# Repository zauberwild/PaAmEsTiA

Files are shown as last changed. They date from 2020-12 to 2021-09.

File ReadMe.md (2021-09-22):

Paamestia
=========
_Teammitglieder: Max, Dominik, André, Arvid

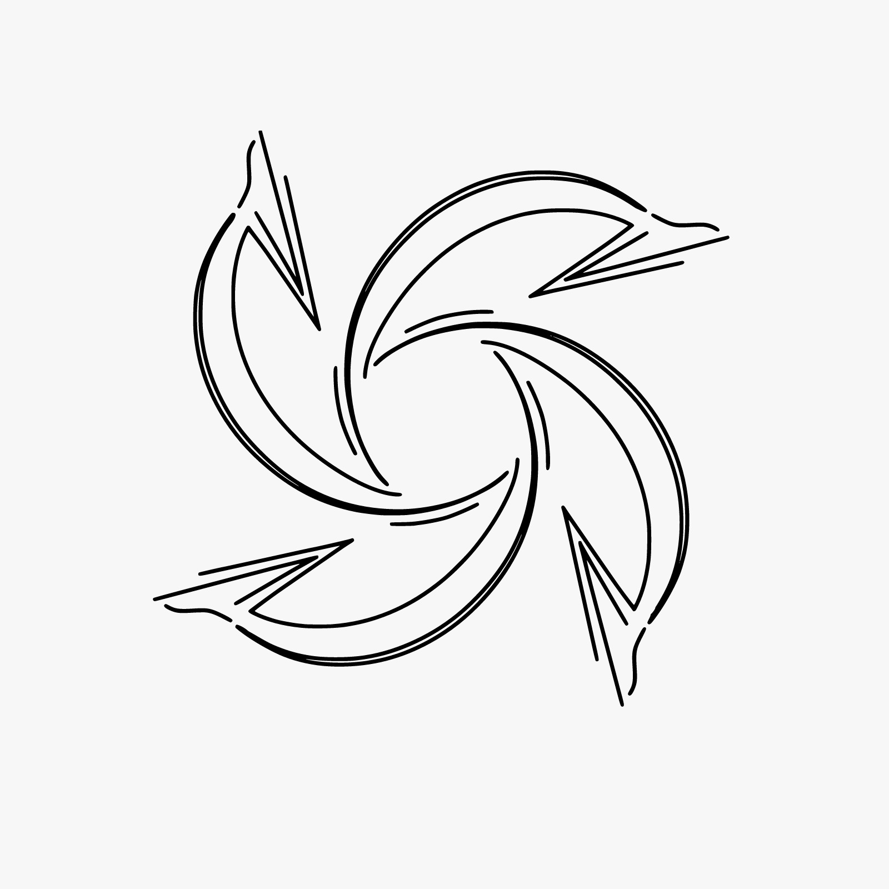
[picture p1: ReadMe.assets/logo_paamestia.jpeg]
logo_paamestia


Info
----

In diesem Repository sind alle Dateien, Quellcodes, etc. für das Praxisprojekt für Fach Praxis im BGT an der BBS.  

Bei dem Projekt handelt es sich um eine Cocktail-Mischmaschine, bei der man ein Rezept auswählt und dies automatisch gemischt wird.
Außerdem soll es möglich sein, selber frei zu mischen und Rezepte zu importieren. 

---

Software (./code)
-----------------
Geschrieben wurde der Quellcode in Python, da diese relativ einfach anzuwenden ist und für den Raspberry Pi gut geeignet ist
Der Quellcode besteht aus mehreren Dateien, denen verschiedenen Aufgaben zukommen. Die Datei media_lib.py kümmert sich um alles grafische und was die Darstellung betrifft, io_lib.py kümmert isch um den direkten Input (Taster) und Output (Ventile und Pumpe) und drinks_lib.py ist u.a. für die Verwaltung der Rezepte und Getränke zuständig. Genauere Informationen zu dem Quellcode finden sich außerdem im Ordner `/documentation/Sourcecode + System`.  

---

Hardware
--------
Das Hirn des gesamten Projekts ist ein Raspberry Pi, einem Einplatinencomputer, der neben Standard-Anschlüssen, wie USB und HDMI auch über GPIO-Pins (_**G**eneral-**P**urpose-**I**nput-**O**uput-Pins_) verfügt. Diese werden dazu verwendet um die Taster auszulesen, und die Ventile anzusteuern. Die Ansteuerung erfolgt dabei über zwei Relais-Boards, um die hohe Stromaufnahme nicht direkt über den Raspberry Pi zu leiten.  
Für das Bild wird ein alter 3/4-Monitor verwendet, auf dem die grafische Benutzeröberfläche angezeigt wird.  
Die Stromversorgung gestaltete sich etwas schwieriger, weil die Pumpe und Ventile mit 12V betrieben werden müssen, Der RasPi aber nur mit 5V. Dafür wurde erst ein 12V-Netzteil verwendet, und zusätzlich ein Step-Down-Converter, der die Spannung für den RasPi auf 5V runterregelt.  
Zur Konstruktion wurden Alu-Profile als Rahmen verwendet, für die Abdeckung Blech. Zur Montage einiger Bauteile wurden außerdem Halterungen 3D-gedruckt, verwendet wurde dafür der Anycubic Mega S mit dunkelgrauem PETG und blauem PLA.  
_Weitere Informationen, Schematiken und CAD-Dateien sind im `documentation`-Ordner zu finden_

### BOM  
In dieser Liste sind hauptsächlich nur die elektronischen und mechanischen Bauteile aufgelistet. Zusätzliche Meterialien, wie Alu-Profil-Schienen werden natürlich ebenfalls benötigt.

- Raspberry Pi 3(b) ([Amazon](https://www.amazon.de/Raspberry-Pi-Model-ARM-Cortex-A53-Bluetooth/dp/B01CD5VC92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))
- Magnetventile (6 Stück, Öffner)
- Schlauch
- Schlauchverbinder
- Relais-Board (insgesamt 7 Relais, [Amazon](https://www.amazon.de/AZDelivery-8-Relais-Optokoppler-Low-Level-Trigger-Arduino/dp/B07CT7SLYQ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ÅMÅŽÕÑ&crid=1XKVNJ5KDLTPH&dchild=1&keywords=azdelivery+relay&qid=1607777597&sprefix=azdeliver%2Caps%2C275&sr=8-8))
- Schlauchpumpe ([Amazon](https://www.amazon.de/Schlauchpumpe-Flüssigkeitspumpe-Schlauchwasserpumpe-Silikonschlauch-Pharmazeutika/dp/B07TVDXJQN))
- Silikonstopfen ([Amazon](https://www.amazon.de/Tuuters-Silikonstopfen-Konische-Abdeckstopfen-Gummistopfen/dp/B01LWOXOLZ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ÅMÅŽÕÑ&crid=11L4LGF9305AW&dchild=1&keywords=silikonstopfen&qid=1607778777&sprefix=silikonstopf%2Caps%2C253&sr=8-5&th=1))
- Taster (6 Stück)
- 12 V Netzteil ([Amazon](https://www.amazon.de/Netzteil-Transformator-Universelles-AC110-240V-Geeignet/dp/B0871TVVRR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))
- Step-Down-Converter (aus eigenem Lagerbestand, zu finden aber zum Beispiel hier: [Amazon](https://www.amazon.de/Stromversorgung-Spannungsregler-Abw%C3%A4rtswandler-Hocheffizienter-Einstellbares/dp/B07F38DJLS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))

Filamente:  
- [DasFilament PETG Anthrazit](https://www.dasfilament.de/filament-spulen/petg-1-75-mm/438/petg-filament-1-75-mm-anthrazit-v2?c=21)
- [Janbex PLA Blau](https://www.amazon.de/JANBEX-Filament-Drucker-Vakuumverpackung-Schwarz/dp/B08MC7LQZR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)

Credits
-------

Dieses Projekt steht unter der MIT-Lizenz (komplette Lizenz [hier](https://github.com/zauberwild/paamestia/blob/main/LICENSE))

### verwendete Module:

- [`pygame`](https://www.pygame.org/news) (und `pygame.freetype`)
- [`opencv`](https://opencv.org/) (und [`numpy`](https://numpy.org/))
- [`tkinter`](https://docs.python.org/3/library/tkinter.html)
- `os`, `time` und `pathlib`
- [`gpiozero`](https://github.com/gpiozero/gpiozero)

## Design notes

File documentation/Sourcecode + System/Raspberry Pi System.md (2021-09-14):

# Raspberry Pi System

## Autostart des Skripts

"Desktop"-Datei (Pfad: `/home/pi/.config/autostart/paamestia-auto.desktop`):  

`[Desktop Entry]`
`Name=Paamestia-Auto`
`Comment=Autostart Script for PaAmEsTiA`
`Type=Application`
`Exec=python3 /home/pi/paamestia/code/paamestia.py`
`Terminal=true`

## Steuerung

Wird mittels Datei `code/src/.windows` angeschaltet

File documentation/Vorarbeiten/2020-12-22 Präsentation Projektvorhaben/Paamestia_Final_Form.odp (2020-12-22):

## Project: Paamestia

Ein Projekt von:

Andre Milling, Dominic Kosin,

Arvid Randow und Max Schiemann

## Gliederung

- Überblick
- Technische Zeichnungen
- Programmierung
- Design
- Netzplan
- Materialliste + -kosten

## Überblick

- Getränkemischmaschine
- Erweiterbare Rezeptliste
- Getränke mischen
  - Nach Rezept
  - Nach Mischverhältnis

## 3D-modell

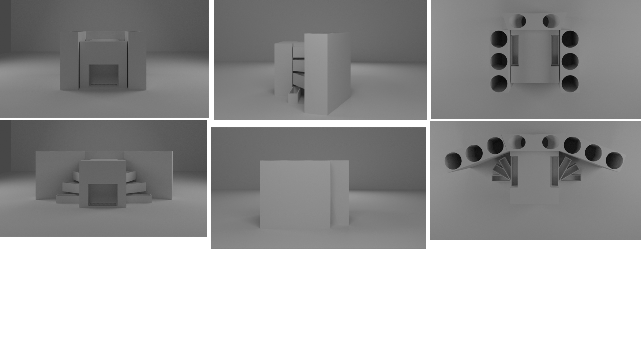
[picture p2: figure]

## Technische Zeichnungen

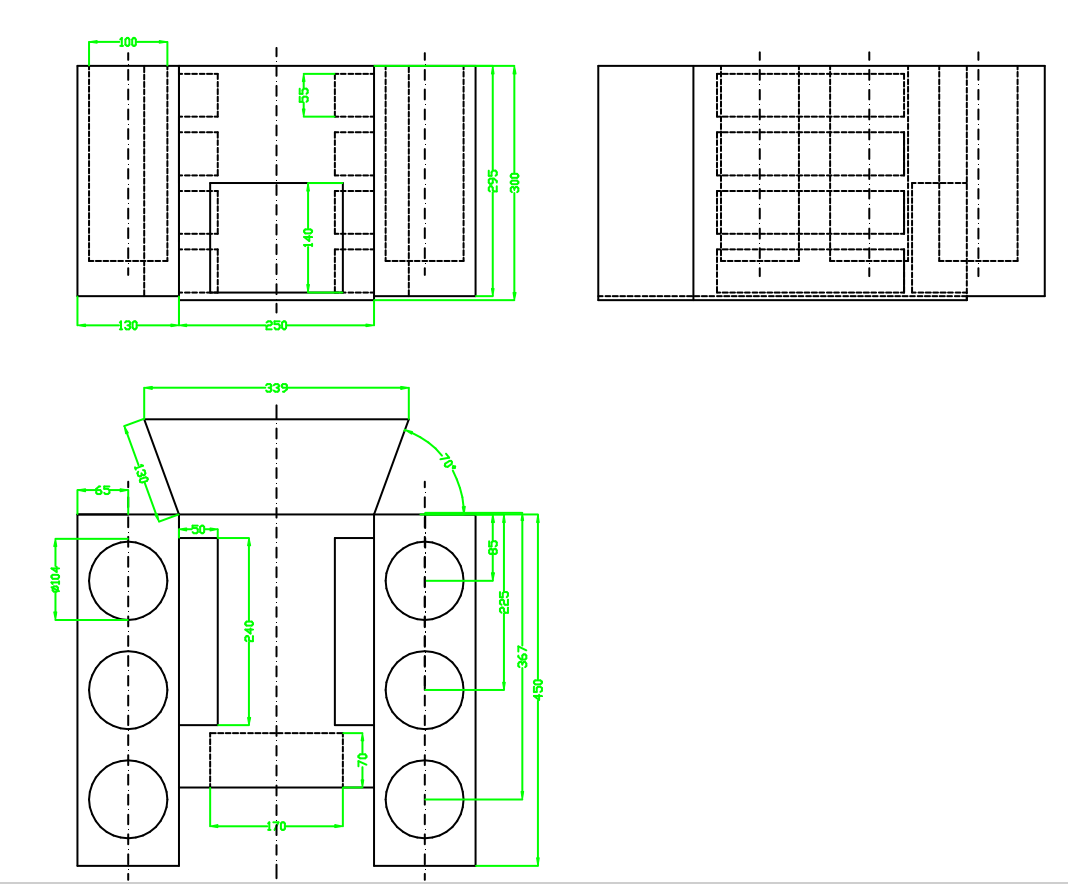
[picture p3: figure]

## Kontaktplan

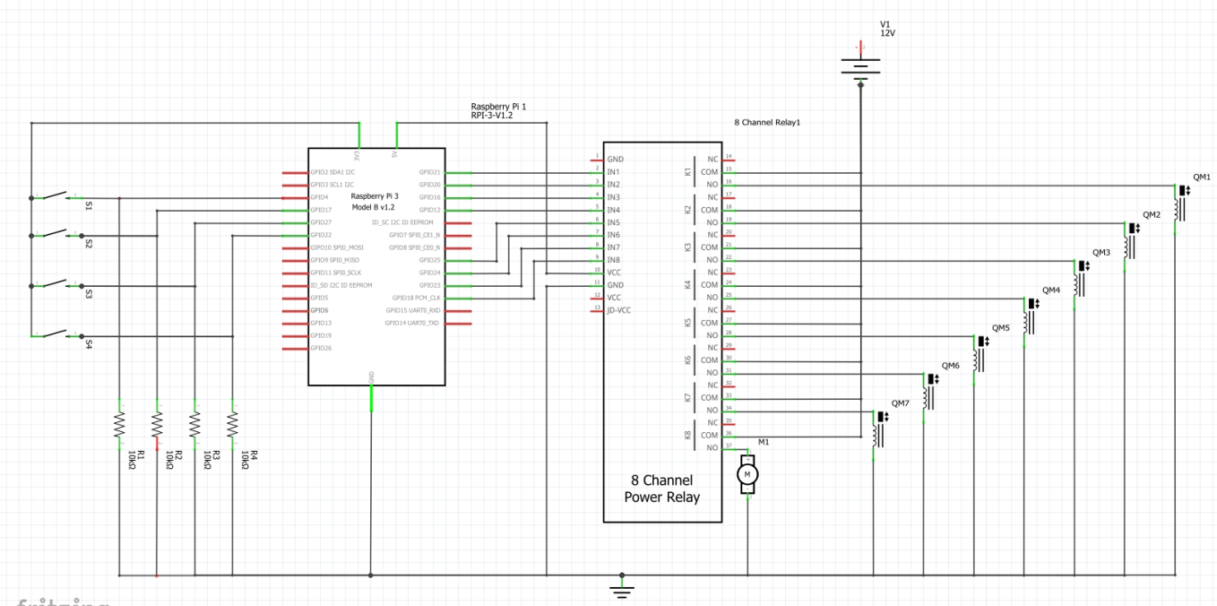
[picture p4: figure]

## Programmierung

- Aufbau
  - Einstellungen (Auswahl von angeschlossenen Getränken)
  - Rezeptauswahl
  - Frei mischen

## Design

- Bar Design
- Barkeeper leitet einen durchs Programm

## Zeitliche Planung

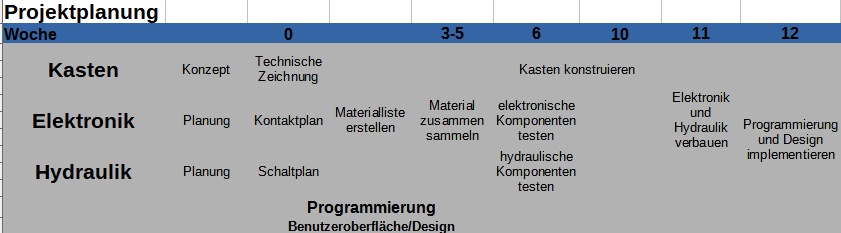
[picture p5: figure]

## Material+ -kosten

Teil | Stückpreis | Menge | Gesamtpreis
Raspberry Pi | 33,60€ | 1 | 33,60€
Magnetventile | 3,40€ | 7 | 23,80€
Silikonschlauch | 9€ | 2 | 18€
Relais Board | 7,50€ | 1 | 7,50€
Schlauchpumpe | 10€ | 1 | 10€
Verbindungsstücke | 10€ | 1 | 10€
Silikonstopfen | 21€ | 1 | 21€
Taster | 9€ | 1 | 9€
Trafo | 10€ | 1 | 10€
Summe | | | 142,90€

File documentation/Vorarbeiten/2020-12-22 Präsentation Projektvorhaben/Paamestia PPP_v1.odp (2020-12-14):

## Project: Paamestia

Ein Projekt von:

Andre Milling, Dominic Kosin,

Arvid Randow und Max Schiemann

## Gliederung

- Überblick
- Technische Zeichnungen
- Programmierung
- Design
- Netzplan
- Materialliste + -kosten

## Überblick

- Getränkemischmaschine
- Erweiterbare Rezeptliste
- Getränke mischen
  - Nach Rezept
  - Nach Mischverhältnis

## 3D-modell

- Weil flex

## Technische Zeichnungen

- Vllt acuh elektronikplan
- Drei ansichten
- Maybe isometrisch

## Technische Zeichnungen

- Vllt acuh elektronikplan
- Drei ansichten
- Maybe isometrisch

## Programmierung

- Raspberry Pi
- Python

## Design

- Bar Design
- Barkeeper leitet einen durchs Programm

## Netzplan (zeitplanung)

- So wie bei BGT 18
- Muss ich noch nachfragen

## Material+Kosten

Teil | Stückpreis | Menge | Gesamtpreis
Raspberry Pi | 33,60€ | 1 | 33,60€
Magnetventile | 3,40€ | 7 | 23,80€
Silikonschlauch | 9€ | 2 | 18€
Relais Board | 7,50€ | 1 | 7,50€
Schlauchpumpe | 10€ | 1 | 10€
Verbindungsstücke | 10€ | 1 | 10€
Silikonstopfen | 21€ | 1 | 21€
Taster | 9€ | 1 | 9€
Trafo | 10€ | 1 | 10€

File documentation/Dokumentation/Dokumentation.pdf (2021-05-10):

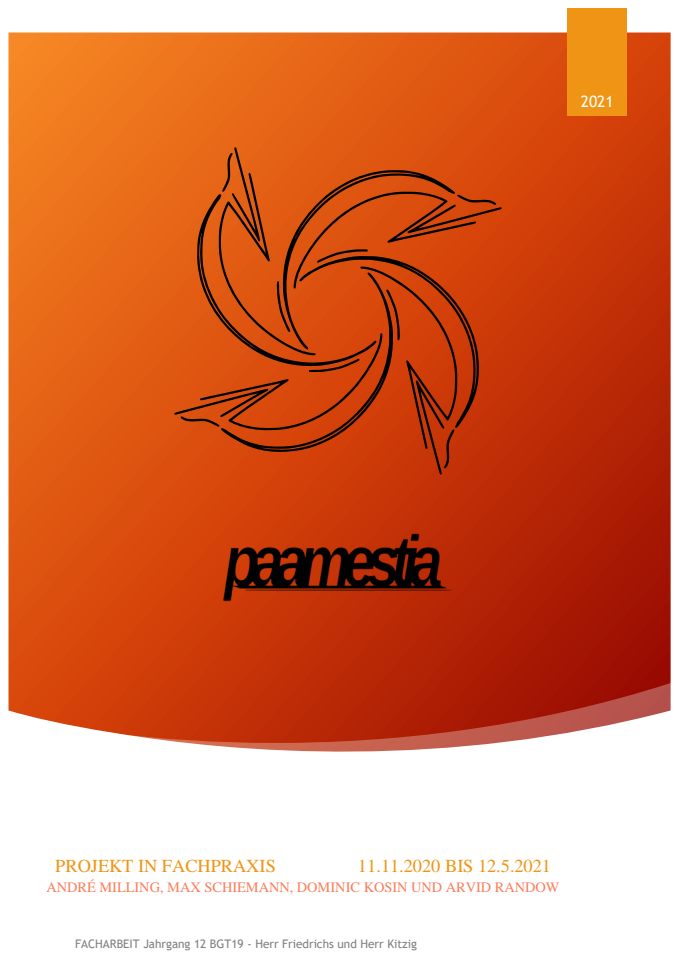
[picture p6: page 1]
PROJEKT IN FACHPRAXIS; 11.11.2020 BIS 12.5.2021

ANDRÉ MILLING, MAX SCHIEMANN, DOMINIC KOSIN UND ARVID RANDOW

FACHARBEIT Jahrgang 12 BGT19 - Herr Friedrichs und Herr Kitzig

INHALTSVERZEICHNIS

Abbildungsverzeichnis | c

ABBILDUNGSVERZEICHNIS

1. EINLEITUNG

In dem Beruflichen Gymnasium Schwerpunkt Mechatronik werden neben den allgemeinen Fächern wie Mathe, Deutsch oder Englisch auch Inhalte und Kompetenzen im Bereich Mechanik, Elektrotechnik und Informatik vermittelt. Zusätzlich beinhaltet der Lehrplan die Umsetzung eines praktischen Projektes, in denen man die erworbenen Kompetenzen einfließen lässt.

2. PROJEKT

Ein Projekt ist ein zielgerichtetes, einmaliges Vorhaben, das aus einer Anzahl abgestimmter, gesteuerter Tätigkeiten besteht und durchgeführt werden kann. Dabei ist zu beachten, dass man bestimmte Vorgaben wie Zeit, Ressourcen (Finanzierung, Personal oder Produktionsbedingungen), Qualität und ein Ziel erreichen muss. Hilfreich ist hier die sogenannt S.M.A.R.T. Methode, um das Projekt in eine geordnete Bahn zu lenken.

S. Spezifisch | „Spezifisch“ steht für eine konkrete und unmissverständliche Aussage, die genau definiert, was wir erreichen wollen.
M. Messbar | „Messbar“ bedeutet, dass Kriterien festgelegt werden, an denen wir das Erreichen des Zieles Objektiv überprüfen können.
A. Attraktiv | „Attraktiv“ bedeutet, dass die Ziele von allen Beteiligten akzeptiert werden muss. Ziele müssen ambitioniert, jedoch nicht unerreichbar sein.
R. Realistisch | Das Ziel muss für uns machbar sein. Unsere Ziele müssen fordernd, aber nicht utopisch sein. Zu hoch gesteckte Ziele würde am Ende ent- täuschen.
T. Terminiert | Das Projekt muss ein Ende, also ein Abgabetermin aufweisen.

Wir haben als Kriterium erhalten, dass das Gerät mechanische Komponenten, elektronisch steuerbar und eine Informationsverarbeitung benutzen muss. Das Budget soll 150€ nicht überschreiten.

3. PROJEKTIDEE

Unsere erste Idee war es, einen Flipper zu entwickeln, welches eine Themenwelt mit beweglichen Komponenten beinhalten sollte. Besonders Dominic war davon angetan, da er dadurch sein Portfolio in grafischen Gestaltungen erweitern konnte. Außerdem waren wir im Besitze eines 3D-Druckers. Des Weiteren sollte der Flipper bestimmte Aktionen bei bestimmten Bedingungen durchführen und sie auf einen Bildschirm grafisch untermalen. Erste Skizzen und Pläne waren schon vorhanden. Jedoch mussten wir des Projekts recht schnell verwerfen, da sich im Rahmen der Komponentensuche ergeben hat, dass der Kauf dieser schnell den Finanziellen Rahmen gesprengt hätte. Mechanische Flipper werden nur noch in weniger Stückzahl produziert. Deswegen sind sie eher Sammlerstücke geworden und die einzelnen Komponenten sind recht hochpreisig.

Beim einem weiteren, eher gemütlichen, Beisammensitzen mit „Erfrischungsgetränken“ ist uns die Idee einer Getränkemischmaschine gekommen.

4. GEPLANTE FUNKTION UND ZIELSETZUNG

Die Maschine soll aus einer Anzahl von Vorgefertigten Rezepten ein Mischgetränk autonom in ein Glas geben.

Dabei sind die Flaschen seitlich kopfüber aufgehängt, und mit einem Schlauchsystem an Magnetventilen angebracht. Die Magnetventile sollen durch ein Programm, welches auf einer kleinen Platine vorhanden ist, angesteuert werden. Die Flüssigkeit soll von den Ventilen in eine Mischbatterie geleitet werden. Eine Schlauchpumpe soll für ein Transport der Flüssigkeit sorgen. Die Flaschen sollen austauschbar sein. Eine Wasserflasche soll die Schläuche regelmäßig reinigen.

Auf einen Monitor soll eine visuelle Menüführung einen durch das Programm führen. Einige Taster sollen die Steuerung durch das Menü ermöglichen.

Man kann sich auch das Getränk manuell mischen.

5. MODULE (PROJEKTBESTANDTEILE)

5.1.PLANUNG

Da wir schon eine ungefähre Vorstellung hatten, welche Komponenten wir im Groben benötigen, mussten wir überlegen, wie wir das Gerät aufbauen wollen. Dabei wurde geplant, dass sich insbesondere die elektrischen Komponenten in einen separaten Kasten recht weit oben befinden sollen. Dadurch soll verhindert werden, dass im Fall von Auslaufen von Flüssigkeit die Elektronik Schaden nimmt. Die Flaschen werden seitlich an den mittleren Kasten untergebracht. Außerdem ist geplant, dass sich die Seiten-Komponenten als Flügel konzipiert werden, damit man durch das Aufklappen besser an die Flaschen und deren Schlauchverbindung rankommt. Anhand einer ersten groben Skizze hat Dominic einen ersten Entwurf über das Aussehen des Gerätes entworfen, welches wir als Gruppe zugestimmt haben.

Daraufhin wurde eine erste technische Zeichnung angefertigt, in denen schon die ersten genauen Bemaßungen angegeben wurde.

5.2.ERMITTLUNG DER KOMPONENTEN

Nachdem wir unseren ersten Konzepten grünes Licht gegeben haben, mussten wir uns überlegen welche Komponenten und Materialien für den weiteren Bau des Projektes benötigen. Dabei haben wir differenziert, für welche Bereiche wir die Materialien benötigen.

5.2.1. KONSTRUKTIONSBEZOGENE KOMPONENTEN

Unter konstruktionsbezogenen Komponenten verstehen wir alle Teile, die dafür sorgen, dass das geplante Gerät eine Stabilität erhält. Dazu gehört ein Konstruktionsrahmen, Verschalungen und andere Komponenten, die zur Befestigung anderer Bauteile benötigt werden.

Rahmen

Da wir planen, einiges an Gewicht in Form von Flaschen mit Flüssigkeiten in das Gerät aufzuhängen, haben wir beschlossen, dass die Konstruktion einen stabilen Rahmen erhalten soll. Als Material haben wir uns Aluminium ausgesucht, weil wir verhindern wollen, dass das Gerät zu schwer wird.

Abbildung 1: erstes Konzept

Nach erster Sichtung des Materials, welches uns die Schule zur Verfügung gestellt hat, sind wir zum Entschluss gekommen, dass die Menge nicht ausreichen wird, um den Rahmen zu vervollständigen. Also haben wir uns dazu entschieden Aluminiumprofile zu bestellen. Wir wählten „Aluminiumprofil 20x20 Nut 6 B-Typ“.

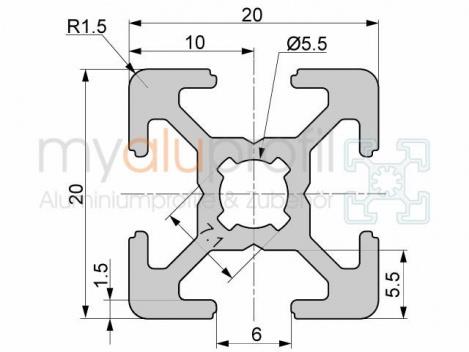
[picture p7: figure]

Als Menge haben wir Profile mit 6 Meter Länge vorgesehen, dabei haben wir recht großzügig Verschnitt mit eingerechnet, da wir gerne im Falle von Fehlern genügend Profile zur Verfügung haben wollten.

Verschalung

Unsere Entscheidung, eine Verschalung aus Blechen zu konstruieren, hat unter anderem ästhetische Gründe. Wir planten einen abgeschlossenen Kasten, wo man das Innenleben nur zu sehen bekommt, wenn man die Seitenflügel aufklappt. Zusätzlich sollen die Bleche noch als Halterungen von anderen Komponenten wie das Tastenfeld oder Anschluss der Stromversorgung. Als Material wurde verzinktes Stahlblech vorgesehen. Dieses stellt uns die Schule zur Verfügung.

Sonstige Befestigungen

Da wir als Gruppe im Besitz eines privaten 3D-Druckers sind, planen wir Halterungen für die Elektronik und Mechanik auszudrucken. Das erspart es uns, zu komplexe Lösungsansätze bei der Befestigung zu konzipieren. Die Befestigungen werden an die Aluminiumprofile angebracht.

5.2.2. MECHANISCHE KOMPONENTE

Schlauchpumpe

Damit Flüssigkeiten befördert werden kann, benötigen wir eine Pumpe. Wir haben eine Schlauchpumpe gewählt, da sie akkurat Flüssigkeiten befördern kann.

Magnetventile

Um die einzelnen Flaschen anzusteuern und entleeren zu können, haben wir Magnetventile gewählt, die auf einer 12V Arbeitsspannung laufen. Wir benötigen sechs Ventile für die

Abbildung 3: Aluminium-Profil Abbildung 2: Aluminium-Profil im Querschnitt

Flaschen, bestehend aus fünf mit Inhalt für Getränke und eine Flasche mit Wasser, die zur Reinigung dient.

Schlauchsystem

Natürlich müssen die Flüssigkeiten auch transportiert werden. Dazu dient ein einfaches Schlauchsystem, das mit Hilfe von Silikonstopfen an den Flaschen befestigt wird. Die Schläuche werden an den Ventilen befestigt. Auf dem Weg zur Pumpe sollen die Schläuche durch einfache T-Stücke verbunden werden, die dann zur Pumpe führen.

5.2.3. ELEKTRONISCHE KOMPONENTE

Raspberry Pi

Als Gehirn unseres Projektes haben wir uns für einen Raspberry Pi entschieden. Die Raspberry Pis sind Einplatinencomputer, die einerseits dazu in der Lage sind, ein komplettes Betriebssystem und Programme auszuführen, andererseits über Schnittstellen verfügen, mit denen elektronische Bauteile angeschlossen und somit angesteuert, bzw. ausgelesen werden können. Die Entscheidung fiel in erster Linie gegen einen Arduino und für den Raspberry Pi, weil wir eine komplette grafische Benutzeroberfläche implementieren wollten. Dies ist mit einem Arduino nur begrenzt möglich, wohingegen der Raspberry Pi deutlich einfacher im Umgang ist. Außerdem beherrschen die Raspberry Pis die Programmiersprache Python, welche über eine simple Syntax verfügt, und somit die Programmierung des Programms erheblich vereinfacht.

Eingabe / Input

Zur Steuerung sollte die Maschine mit sechs Tastern ausgestattet werden, wovon vier ein Steuerkreuz oder Pfeiltasten repräsentieren, und zwei weitere die Bewegungen durch die Benutzeroberfläche ermöglichen.

Ansteuerung der Mechanik / Output

Da die Magnetventile eine Arbeitsspannung von 12V haben, der Raspberry Pi aber nur 3,3V zur Verfügung stellen kann, benötigten wir Relais. Hier mussten wir insbesondere darauf achten, dass diese mit der geringen Steuerspannung von 3,3V kompatibel sind. Unsere Auswahl fiel schließlich auf Relais-Boards von AZ-Delivery, die außerdem in der Schule zur Verfügung standen.

Anzeigen der Benutzeroberfläche

Schließlich benötigten wir einen Monitor, um die Benutzeroberfläche überhaupt anzeigen zu können. Herr Friedrichs konnte uns hier mit einer großen Auswahl aushelfen und wir haben uns einen möglichst kleinen Monitor ausgesucht, der Platz auf der Maschine finden würde.

5.3.BESTELLUNG

Tabelle 1: Bestellliste

Nr. | Beschreibung | Einzelpreis | Anzahl | Gesamtpreis
1 | Magnetventile | 3,39 € | 7 | 23,73 €
2 | Schlauch und Schlauchverbinder | 8,99 € | 1 | 8,99 €
3 | Zusätzlicher Schlauch | 8,99 € | 1 | 8,99 €
4 | Schlauchpumpe | 11,89 € | 1 | 11,89 €
5 | Silikonstopfen | 20,99 € | 1 | 20,99 €
6 | Taster | 8,99 € | 1 | 8,99 €
7 | Netzteil | 11,99 € | 1 | 11,99 €
8 | Aluminium-Profile | Ca. 60 € | 6m | 60 €
Summe: | | | | 155,57 €

Zusätzliche Materialien, die von der Schule zur Verfügung gestellt wurden:

- Raspberry Pi 3B
- Monitor
- 2x AZ-Delivery 4-fach Relais-Boards
- Verzinkte Stahlbleche
- Schrauben und Muttern

5.4.BAU DES RAHMENS

5.4.1. VORÜBERLEGUNG

Bei der Bemaßung des Rahmens mussten wir uns vorher im Klaren sein, wie das Gerät am Ende aussehen soll. Einmal zurechtgesägt und verbunden sind wir nicht mehr in der Lage, am Grundgerüst Veränderungen vorzunehmen.

Modulnummer | 1
Modulname | Rahmenbau
Ziel des Moduls | Konstruktion eines Grundrahmens
Veranschlagte Zeit | 4h | Benötigte Zeit | 6h
Mitwirkende | André Milling, Max Schiemann
Benutzte Fertigungsverfahren | Benutzte Werkzeuge
Trennen | Sägen | Bandsäge
| Bohren | Tischbohrer mit 6er Bohrer
| Gewindebohren | 6er Gewindeschneider Set
Fügen | Kraftschluss
Welche Probleme sind aufgetreten? | Wie wurden sie gelöst?
Keine vorgefertigten Fügemethoden anwend-bar | Bohrungen durch die Profile

5.4.2. BESTIMMEN DER GRÖSSE

Aus den ersten Skizzen wurde eine erste technische Zeichnung erstellt, die unsere finalen Maße ergeben sollte.

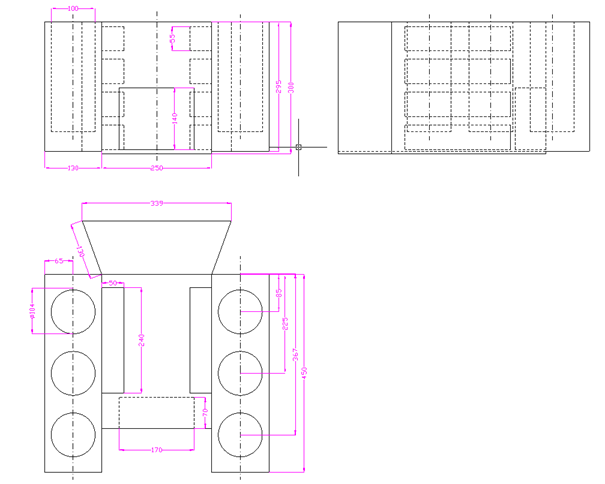
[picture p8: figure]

Abbildung 4: Erste technische Zeichnung
Dabei ist uns aufgefallen, dass wir den Mittelteil um 100mm verbreitern mussten, damit es in etwa so breit ist wie der für uns zur Verfügung stehender Monitor. Dadurch kamen folgende Abmessungen zu Stande:
Mittelteil: | L/B/H: | 350mm/350mm/245mm
Flügelteile: | L/B/H: | 450mm/130mm/295mm

Durch die Breite der Profile von 20mm ergaben sich folgende Abmessungen:

Tabelle 2: Profillängen

Länge | Anzahl
345mm | 4
310mm | 8
295mm | 8
90mm | 8
410mm | 8
5.4.3. ZUSAMMENBAU

Die fertig bemaßten Profile wurden mit einer Bandsäge in Länge zugeschnitten. Das Unterfangen hat sich ein wenig verzögert, weil die dafür vorgesehen Bandsäge falsch arretiert war und nicht im rechten Winkel trennt. Nach Versuchen, das Problem zu lösen, haben wir die Profile mit einer anderen Bandsäge zurechtgeschnitten.

Nach dem Zuschnitt mussten wir in einigen Profilstücken ein Gewinde reinschneiden. Dazu haben wir uns für einen Satz 6er Gewindeschneider entschieden. Dabei sind wir behutsam vorgegangen, weil ein sehr weiches Material bearbeitet wurde. Anschließend wurden an weiteren Profilstücken Bohrungen mit einem 6er Bohrer vorgenommen. Die Bohrungen erfolgten einmal in einem Abstand von 10mm und weiteren 30mm um 90 Grad versetzt. Zum Schluss haben wir die Profile mit 6er Schrauben verbunden. Einige Gewinde mussten wir nochmal nachbessern, weil die Schrauben nicht ordnungsgemäß angezogen haben.

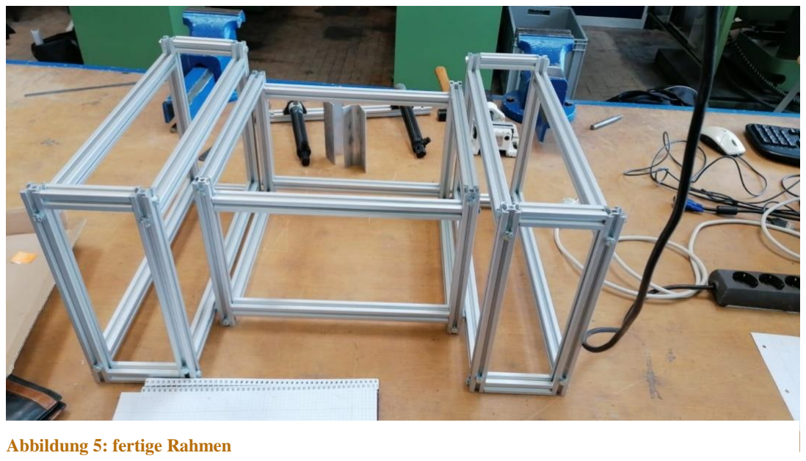
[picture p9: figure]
Abbildung 5: fertige Rahmen

5.5.VERSCHALUNG
Modulnummer | 2
Modulname | Verschalung
Ziel des Moduls | Konstruktion der Außen-hülle
Veranschlagte Zeit | 4h | Benötigte Zeit | 6h
Mitwirkende | André Milling, Max Schiemann
Benutzte Fertigungsverfahren | Benutzte Werkzeuge
Trennen | Schneiden | Schlagschere
| Entgraten | Entgrater, Feile, Kegelsenker
| Bohren | Standbohrmaschine, 7er Bohrer
Fügen | Kraftschluss
Umformen | Biegen
Welche Probleme sind aufgetreten? | Wie wurden sie gelöst?
Durch Rundungen der Aluprofile entstehen Überstände | Bleche ein paar Millimeter kleiner zuge-schnitten
Durch kleinere Bleche keine Maßbe-zugskante mehr möglich; Durch Ungenauig-keit des Rahmens keine akkuraten Bohrun-gen möglich | Nutzung von 7er Bohrern für mehr Spiel; Kegelsenker zur Vergrößerung der Bohrun-gen

5.5.1. PLANUNG DER BLECHZUSCHNITTE

Bei den Bemaßungen der Außenverkleidungen haben wir uns ebenfalls an die Maße aus Kapitel 5.4.2 gehalten. Dabei ist jedoch zu beachten, dass die Profile an den Kanten Rundungen besitzen. Hätten wir die Bleche auf das Maß zugeschnitten, würden sich Überstände ergeben, die eventuell zu Verletzungen führen könnten. So haben wir uns entschieden, die Bleche je 3mm kleiner zu bemaßen.

Wir haben uns dazu entschieden, dem mittleren Kasten einen Boden sowie einen Deckel zu geben. Zusätzlich soll in der Front eine ausreichend große rechteckige Öffnung für das Glas und für die Abdeckplatte des Bedientasten ausgeschnitten werden. In dem hinteren Blech ist ein Loch für die Stromversorgung, sowie eine weitere Öffnung für die Hauptplatine vorgesehen.

Die Verschalung an der Seite haben wir weggelassen, da dadurch der Zugang zum Innenraum des Gerätes gewährleistet wird. Für die Seitenteile haben wir uns überlegt, den Boden wegzulassen, weil es konstruktionstechnisch aufwändiger wäre. Zusätzlich haben die beiden Seitenteile keine Deckel, da man da die Flaschen von oben kopfüber reinsetzt. Eine Seitenwand wurde freigelassen, um den Zugang zu den Flaschen und den Schläuchen zu ermöglichen.

Durch diese Vorüberlegungen entstanden folgende Maße der Blechzuschnitte:

Tabelle 3: Bemaßung der Blechstücke

POSITION | LÄNGE | BREITE | ANZAHL
FRONT/HINTEN | 347mm | 242mm | 2
DECKEL | 347mm | 347mm | 1
BODEN | 387mm | 347mm | 1
FLÜGEL VORNE UND HINTEN | 127mm | 293mm | 4
SEITENTEIL FLÜGEL | 447mm | 293mm | 2
5.5.2. ZUSCHNITT UND MONTIERUNG AM RAHMEN

Die Bleche haben wir nach den ermittelten Maßen mit einer Schlagschere zurechtgeschnitten und anschließend mit einem Entgrater die scharfen Kanten entfernt. Da der Rahmen nicht akkurat lotrecht war und wir keine einheitlichen Maßbezugskanten besaßen, haben wir die Positionen nach „Augenmaß“ angerissen und gekörnt. Um trotzdem alles gut mit Schrauben verbinden zu können, haben wir die Bohrungen eine Nummer größer - 7er Bohrer - angesetzt, damit wir bei der Montage Spielraum hatten. Die Bohrungen wurden mit einem Kegelsenker entgratet. In der Front wurden die geplanten Öffnungen für das Glas und das Schaltpult angerissen, vorgebohrt und mit einer Stichsäge ausgeschnitten. Scharfe Kanten wurden hier ebenfalls entfernt. Dasselbe haben wir für die Rückseite durchgeführt. Da wurde ein größeres Loch für den Zugang der Stromversorgung gebohrt und ein Rechteck für das IO- Panel des Raspberry ausgeschnitten.

Den Boden haben wir etwas länger gewählt, damit wir es je 20mm entlang der kürzeren Kante um 90 Grad biegen können. Dies war nötig, damit man so die Bodenplatte an den Rahmen montieren konnte.

Abbildung 7: Zugeschnittene Bleche | Abbildung 6: vorderes Blech mit Tastenblende

5.6.HALTERUNGEN DER KOMPONENTEN

Um die elektronischen Komponenten an den Rahmen oder an der Verschalung zu befestigen, haben wir einen privat zur Verfügung stehenden 3D-Drucker verwendet, um Halterungen zu drucken.

Modulnummer | 3
Modulname | Halterung der Komponenten
Ziel des Moduls | Bauteile produzieren, die die elektronischen Komponenten sicher am Gehäuse befestigen
Veranschlagte Zeit | So viel wie nötig / Heim-arbeit | Benötigte Zeit | 5h Erstellen, 25h Drucken
Mitwirkende | Arvid Randow
Benutzte Fertigungsverfahren | Benutzte Werkzeuge
Additiv: Fused Deposition Modeling / Schmelzschichtung | 3D-Drucker: Anycubic Mega S

## Benutzte Software

Autodesk Fusion 360 | Erstellung der 3D-Modelle / CAD-Dateien
Ultimaker Cura | Vorbereitung des 3D-Drucks

5.6.1. DESIGN / ERSTELLUNG DER 3D-MODELLE

Im ersten Schritt müssen die Halterungen entworfen werden, wozu wir „Fusion 360“ von Autodesk verwendet haben. Die einzelnen Arbeitsschritte werden hier einmal am Beispiel der Halterung für die Relais gezeigt. Zuerst wird eine Skizze vom Grundriss angefertigt. Die Halterung des Relais-Boards soll an einem Aluminium-Profil befestigt werden, beziehungsweise aufgeschoben werden und das Relais-Board selbst wird auf die Halterung geschoben, sodass es jederzeit wieder entfernt werden kann. In der Abbildung 10 wird das Alu-Profil lila und das Bauteil schwarz dargestellt. Aus diesem Grundriss kann eine Art Rohform „extrudiert“ werden, welche dann weiterbearbeitet werden kann. Hier werden die zusätzlichen Schienen an den Seiten hinzugefügt, und, um Material einzusparen, die Grundfläche ausgeschnitten und durch ein Kreuz ersetzt. Wenn das Modell fertig ist, wird es als Netzdatei im STL-Format exportiert.

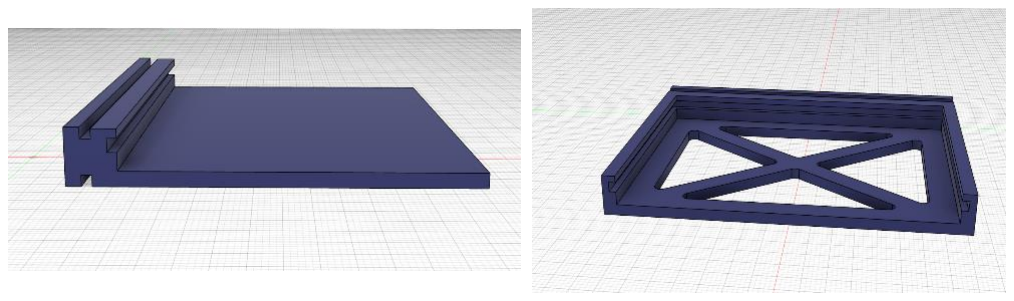
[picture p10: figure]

5.6.2. AUSDRUCKEN

Um ein Modell drucken zu können, muss es „gesliced“ werden. Dazu wird eine spezielle Software benötigt, in diesem Fall Ultimaker Cura. Dieses Programm nimmt die STL-Datei und erstellt daraus Anweisungen für den Drucker. Dabei stehen auch eine Vielzahl von Einstellungen zur Verfügung, die das Verhalten des Druckers und damit die Geschwindigkeit des

Druckes und Qualität des Bauteils beeinflussen. Beispielsweise können die Höhe der Schichten, die Geschwindigkeit oder die Temperatur geändert werden. Das fertig „geslicede“ Modell, also die Anweisungen für den 3D-Drucker, kann danach als G-Code auf einer SD-Karte

Abbildung 10: 2D-Entwurf | Abbildung 9: 3D Entwurf | Abbildung 8: Finales Modell
Abbildung 11: Einstellungen zum Slicing | Abbildung 12: Bedienoberfläche Cura

gespeichert und auf den Drucker übertragen werden. Ein G-Code, oder DIN-Programm ist auf allen CNC-Maschinen, wie zum Beispiel CNC-Fräsen oder 3D-Druckern lauffähig. Er besteht aus einfachen Anweisungen, unter anderen welche Position der Druckkopf anfahren soll.
Bei dem 3D-Drucker handelt es sich um einen FDM-Drucker. Das heißt, dass das Druckmaterial geschmolzen und durch eine Düse auf das Druckbett gebracht wird. Auf diese Weise wird Schicht für Schicht Material aufgetragen, bis der Druck abgeschlossen ist. Abgesehen von der Entfernung von ein paar Kunststoff-Fäden, oder das Entfernen von Stützstrukturen ist normalerweise keine Nachbearbeitung mehr erforderlich, und die Bauteile können direkt eingebaut werden. Für FDM-Drucker gibt es eine Vielzahl von verschiedenen Materialien, wir haben uns hier für PLA und PETG entschieden, da beide Materialien verhältnismäßig einfach zu verarbeiten sind und eine gewisse Stabilität aufweisen. Für die meisten nicht sichtbaren Bauteile verwendeten wir PLA in blau und für die sichtbaren Bauteile aus optischen Gründen PETG in dunkelgrau.
5.6.3. EINBAUEN

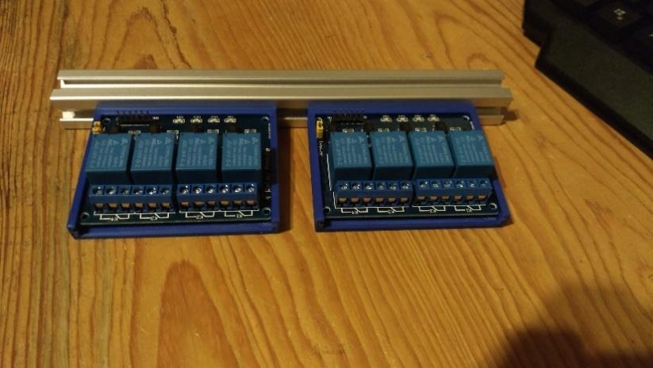
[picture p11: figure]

Die meisten Bauteile können einfach auf die Alu-Profile aufgeschoben werden. Ausnahme sind hier die Halterung für den Raspberry Pi und die Blende für die Taster. Für diese wurden Löcher gebohrt, beziehungsweise geschnitten, wo die Halterungen eingesetzt werden konnten.

Abbildung 13: fertige Halterung | Abbildung 14: Halterung mit Relais-Boards

5.7.ELEKTRONIK

5.7.1. INPUT – TASTER

Die Taster wurden an einer 3D-gedruckten Blende an der Vorderseite befestigt. Um diese Taster auszulesen, haben wir das „gpiozero“-Modul verwendet. Dieses Modul geht standardmäßig davon aus, dass die Taster über den internen Pull-Up-Widerstand des Raspberry Pis ausgelesen werden. Daher konnten wir die Taster einfach an die Input-Pins und an Masse anschließen.

Modulnummer | 4
Modulname | Elektronik
Ziel des Moduls | Komponenten mit Strom versorgen
Veranschlagte Zeit | 3h | Benötigte Zeit | 4.5h
Mitwirkende | Arvid Randow, Max Schiemann, André Milling
Benutzte Fertigungsverfahren | Benutzte Werkzeuge
Löten | Lötkolben
Crimpen | Crimpzange
| Seitenschneider
Welche Probleme sind aufgetreten? | Wie wurden sie gelöst?
Wackelkontakte | Betroffene Stecker neu vercrimpt
Verwendung des internen Pull-Up-wider-standes des Raspberry Pis | Recherche zu Funktionsweise von Pull-Up-Widerständen

5.7.2. OUTPUT – MAGNETVENTILE UND PUMPE
5.7.2.1. BAUTEILE
- Raspberry Pi 3b: Der Raspberry Pi
ist ein Einplatinencomputer. Das heißt, er verfügt über alles, was auch ein normaler Computer hat, also ein Betriebssystem, USB-Anschlüsse, HDMI-Anschlüsse, etc., allerdings befinden sich alle Bauteile auf einer Platine. Zusätzlich dazu hat der
Raspberry GPIO-Pins (General-Purpose-Input-Output-Pins), mit denen,

wie bei den Arduino, andere Bauteile ausgelesen und angesteuert werden können. Diese GPIO-Pins haben eine Arbeitsspannung von 3.3V, er hat aber auch Pins mit einer Spannung von 5V. Er war für unser Projekt perfekt geeignet, weil er einerseits einen Monitor ansteuern kann, und damit eine komplette Benutzeroberfläche möglich ist, bietet andererseits aber auch Möglichkeiten, elektronische Bauteile anzusteuern und auszulesen.
- AZ-Delivery Relais-Board: Wir verwenden
diese Relais-Boards, um die Pumpe und die
Magnetventile anzusteuern, da sich die Arbeitsspannung des Raspberry Pis von der der Aktoren unterscheidet. Da die benötigte Spannung im Steuerkreis der Relais immer noch 5V beträgt, verfügt das Board über Optokoppler, die ein Signal von einem Stromkreis mit 3.3V an einen Stromkreis mit 5V weiterleiten können. Allerdings hat sich nach einiger Recherche und Untersuchung der Platine herausgestellt, dass diese
Optokoppler das Signal anscheinend negieren. Daher mussten wir auch selbst das Sig-

nal vom Raspberry Pi nochmal negieren, damit sich die Relais wie gewünscht verhalten.
- Pumpe: Bei der Pumpe handelt es sich
um eine Schlauchpumpe. Das heißt,
dass ein Schlauch durch mehrere Rollen zusammengedrückt wird. Auf diese Weise kommt die Flüssigkeit nie mit mechanischen Teilen in Berührung,

Abbildung 15: Raspberry Pi 3 B

Abbildung 16: AZ-Delivery 4x Relais-Board

Abbildung 17: Schlauchpumpe

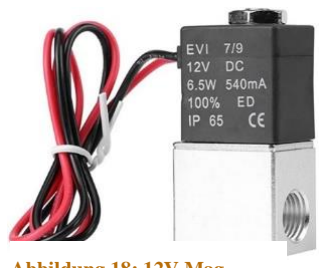
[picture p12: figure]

Abbildung 18: 12V Magnetventil weshalb solche Pumpen sehr hygienisch sind und zum Beispiel in der Medizin Anwendung finden.
- Magnetventil: Unsere Magnetventile sind Öffner und werden mit 12V Gleichstrom versorgt. Wir haben insgesamt sechs Ventile eingebaut, fünf davon für Getränke, das sechste ist für Reinigungswasser, um die Schläuche zwischen den Mischvorgängen zu reinigen.
5.7.3. STROMVERSORGUNG
- Step-Down-Converter: Unser Projekt wird mit einem 12V-Netzteil versorgt, allerdings darf der Raspberry Pi nur mit maximal 5V versorgt werden. Deshalb benötigten wir einen Step-Down-Converter, um die Spannung herunterzuregeln.
- Verteilung: Da wir mehrere Bauteile verwenden, die Strom benötigen, brauchten wir auch einen möglichst einfachen, aber auch eleganten und sicheren Weg, die Leitungen aufzuteilen. Aus diesem Grund
haben wir Herrn Janovski um Rat
gebeten. Er konnte uns mit einer
Hutschiene und dazugehörige Klammern ausstatten. Die Klammern können an der Hutschiene angebracht werden und mittels spezieller Brücken miteinander verbunden werden. Außerdem bekamen
wir Aderendhülsen, die wir an den

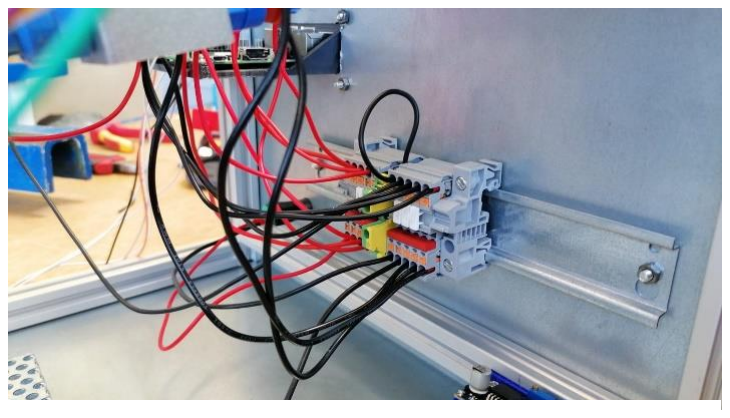
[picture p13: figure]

Leitungen anbringen konnten, um ein Abbrechen einzelner Adern zu verhindern.
- Bei der Farbkodierung haben wir uns darum bemüht, dass wir uns an Standards und Normen halten. Allerdings war dies durch die uns zur Verfügung stehenden Kabel und einzelner Planänderungen nicht immer möglich, weshalb die Kodierung möglicherweise abweicht. Im Folgenden haben wir die Kodierung aufgelistet, aufgeteilt nach Stromversorgung, Ausgängen und Eingängen:

Abbildung 19: Step-Down-Converter LM2596

Abbildung 20: Montage der Hutschienen und Stromverteilung

Spannungsversorgung

Typ | Farbe
+12V | Rot
+ 5V | Orange
GND | Schwarz
GND Taster | Gelb

Ansteuerung der Relais

Typ | Farbe
Pumpe | Blau
Ventile | Weiß / Grau

Auslesen der Taster

Taster | Farbe
Vor / Zurück | Grün

Links /
Rechts

Lila

Hoch / Runter

Blau

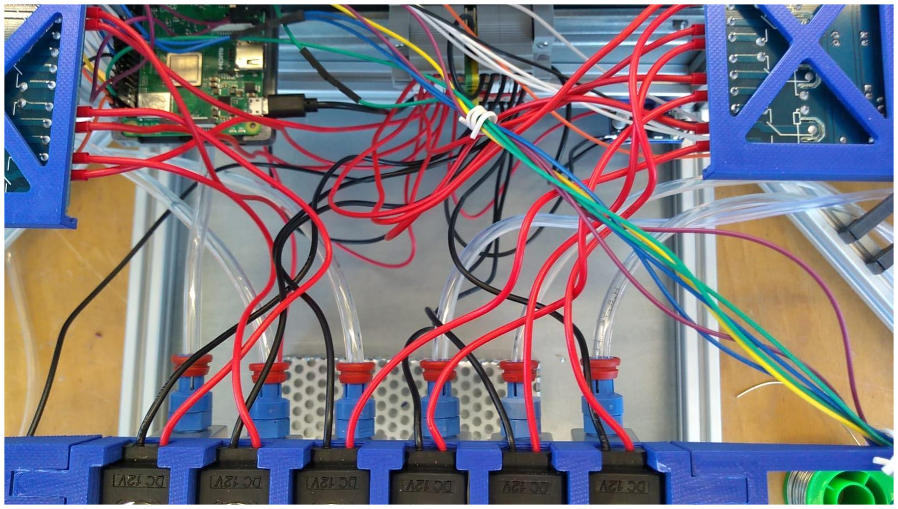
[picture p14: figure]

Abbildung 21: Kabelmanagement

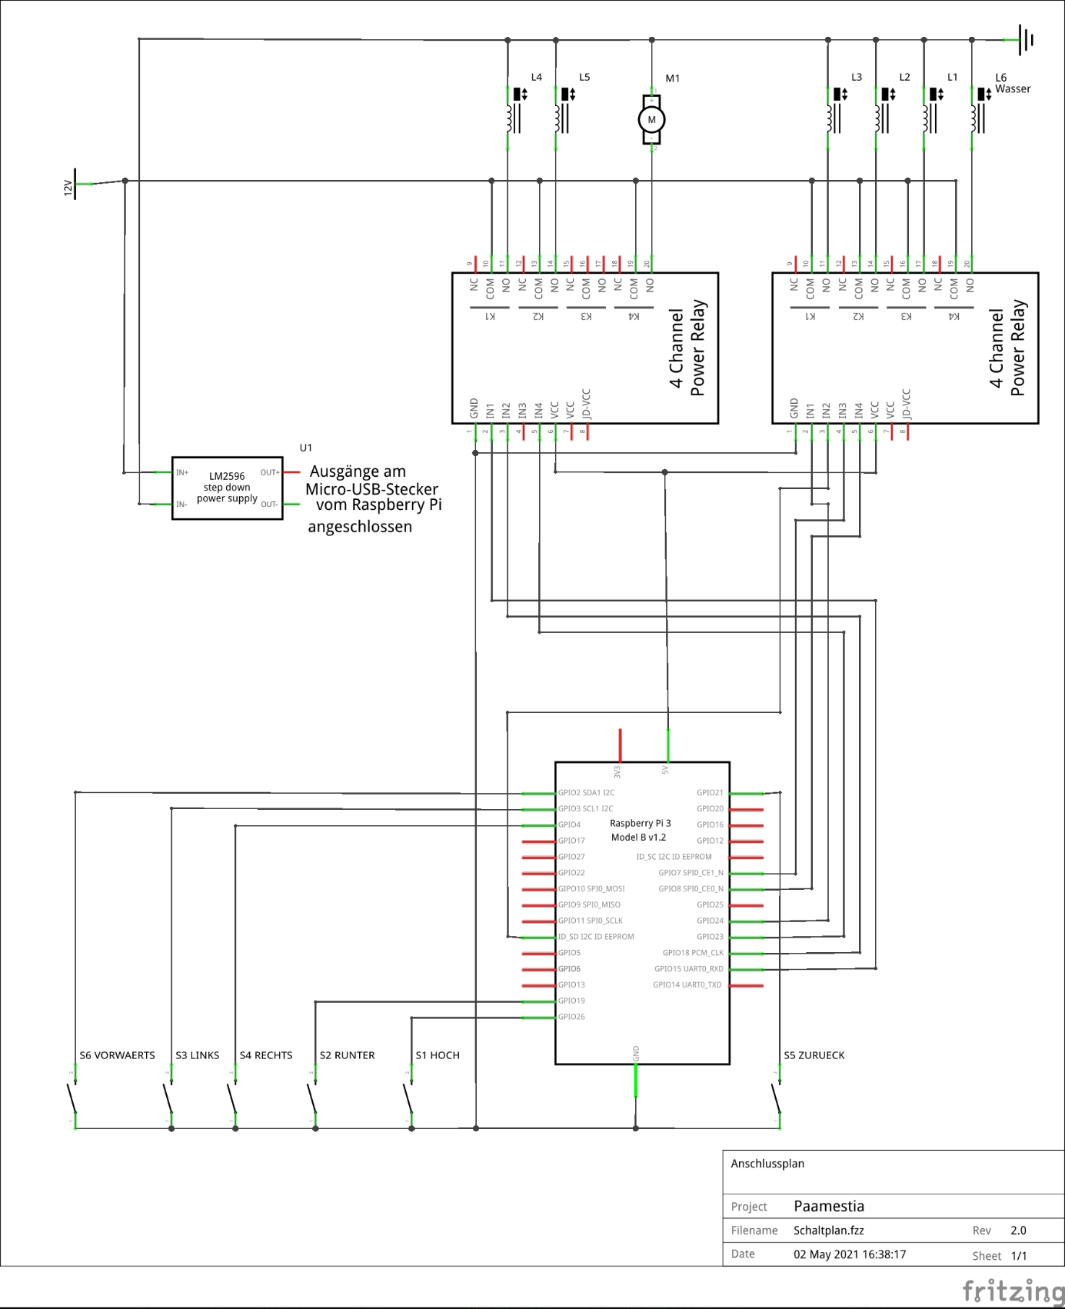
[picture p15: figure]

Abbildung 22: Schaltplan

5.8.SCHLAUCHSYSTEM

Das Schlauchsystem soll das Wasser von den Flaschen zu den Ventilen und anschließend zur Pumpe befördern. Als Anschluss für die Flaschen haben wir einfach Silikonstopfen gewählt, in denen wir jeweils ein Loch gebohrt haben. In die Löcher wurden Schläuche eingeführt. An den Ventilen haben wir Schnellspannsysteme für Pneumatik-Schläuche gewählt, damit wir die

Modulnummer | 5
Modulname | Schlauchsystem
Ziel des Moduls | Konstruktion und Anbrin-gung der Flüssigkeitsfüh-renden Komponenten
Veranschlagte Zeit | 1.5h | Benötigte Zeit | 1.5h
Mitwirkende | André Milling, Max Schiemann, Arvid Randow
Benutzte Fertigungsverfahren | Benutzte Werkzeuge
Schneiden | Seitenschneider
Welche Probleme sind aufgetreten? | Wie wurden sie gelöst?
Verschiedenen Lecks, unter anderen an den Ventilen | Konnten keine Lösungsansätze finden
Mangelnde Ansaugkraft der Pumpe, unter anderen verursacht durch einströmende Luft in das Schlauchsystem | Konnten keine Lösungsansätze finden

Schläuche von den Flaschen anbringen konnten. Auf der Pumpenseite haben wir mit recht Kurzen Teilstücken vom Schlauch und T-Stücken aus Kunststoff eine Art Mischbatterie entwickelt. Dabei haben wir darauf geachtet, dass der Teil, durch was das Wasser für die Reinigung fließ, den längsten Weg nehmen muss.

Eine Problematik stellten hierbei Lecks in dem Schnellspannsystem dar, welches nur für Luft ausgelegt ist, und daher Probleme mit Flüssigkeiten verursacht. Dieses Problem konnten wir jedoch durch Zeitmangel und der für unseren Einsatz nicht geeigneten Bauteile nicht mehr lösen.

Abbildung 23: Mischbatterie | Abbildung 24: Schlauchsystem / Anschlüsse für die Getränke

5.9.PROGRAMMIERUNG
Modulnummer | 6
Modulname | Programmierung
Ziel des Moduls | Ein funktionierendes Pro-gramm erstellen, welche die Bedienoberfläche und die elektronischen Bauteile miteinander verknüpft
Veranschlagte Zeit | So viel wie nötig / Heim-arbeit | Benötigte Zeit | Ca. 150-200h
Mitwirkende | Arvid Randow
Benutzte Software | Benutzte Python-Module
Programmiersprache: Python | Benutzeroberfläche: Pygame, OpenCV, Tkinter
Entwicklungsumgebung: Visual Studio Code und Genius | Steuerung der Ein- und Ausgänge: gpiozero
Betriebssystem des Raspberry Pis: Raspbian OS | Zusätzliche Module: numpy, time, pathlib, os

Zusätzliche Software: GitHub und SSH

Welche Probleme sind aufgetreten? Wie wurden sie gelöst?

Der Quellcode ist für dieses Projekt zu umfangreich, um ihn hier komplett einzufügen. Daher haben wir ihn sowohl im Original als auch als HTML-Datei hinterlegt und werden hier nur auf die einzelnen Bestandteile eingehen.

5.9.1. SYSTEM: RASPBIAN OS

Da der Raspberry Pi ein vollständiger Computer ist, benutzt er auch ein Betriebssystem und kann nicht wie ein Arduino programmiert werden. Als Betriebssystem haben wir uns für Raspbian OS entschieden, da es das offizielle Betriebssystem für den Raspberry Pi ist und leicht zu verwenden ist. Raspbian OS basiert auf der Linux-Distribution Debian und bietet daher eine komplette Desktop-Umgebung. Um unser Programm auszuführen, war lediglich die Installation von Python und den benötigten Python-Modulen notwendig. Außerdem sollte das Programm automatisch starten, wenn der Raspberry Pi hochfährt. Dazu gibt es in Linux einen speziellen Ordner, in dem nach ausführbaren Verknüpfungen gesucht wird. Dort mussten wir lediglich eine eigene Verknüpfung hinzufügen.

5.9.2. SOFTWARE

Als Programmiersprache haben wir Python verwendet, da diese einfach zu verwenden ist und viele Möglichkeiten, vor allem in Verbindung mit dem Raspberry Pi, bietet. Da unser Programm sehr umfangreich wurde, haben wir es in mehrere Dateien aufgeteilt und als Module verwendet. Dazu kamen weitere Module, die weitere Aufgaben übernommen haben.

Durch den Umfang und der damit einhergehenden Unübersichtlichkeit fügen wir hier nicht den kompletten Quellcode ein, sondern erklären nur die einzelnen Bestandteile:

- globals.py: Diese Datei beinhaltet Variablen und Objekte, die von mehreren Dateien benötigt werden. Dazu gehören zum Beispiel die Breite und Höhe des Fensters oder die Framerate. Außerdem gibt es die Variable prog_pos. Sie speichert das aktuelle ausgewählte Menü. Diese Variable besteht aus zwei Textzeichen. Das erste speichert den Modus oder die ausgewählte Position im Hauptmenü, das zweite die genaue Position bei der Rezeptwahl, dem freien Mischen oder den Einstellungen.
prog_active = True | # set to False to end program
FPS = 24 | # frames per second
W, H = 800, 600 | # width and height of the window
prog_pos = 'i' | # saves current position in program flow
Begrenzte Kapazitäten des Raspberry Pis | Verringerung der Bildschirmauflösung,
sowohl beim Arbeitsspeicher als auch der | Verwendung eines effizienteren Python-
Geschwindigkeit | Moduls

- paamestia.py: Das ist der eigentliche Python-Skript, der die grundsätzliche Struktur des Programmes kontrolliert und unter anderem die richtige Funktion ausführt, je nach dem in welchem Menü man sich gerade befindet. In der Abbildung ist kurzer Ausschnitt dieser Zuordnung gezeigt.

# run external methods according to prog_pos

if gl.prog_pos == 'i': | # intro

ui.intro()

elif gl.prog_pos == 'm': | # main menu

ui.main_menu()

elif gl.prog_pos[0] == 'f': | # free mixing
if gl.prog_pos[1] == 'c': | # mix cocktail

ui.free_choose()

elif gl.prog_pos[1] == 'o': | # output

ui.free_output()

- media_lib.py: Hier sind mehrere Klassen definiert, mit denen die grafische Oberfläche aufgebaut werden kann. Wir haben hier zum größten Teil das Modul „Pygame“ verwendet, welches in erster Linie zur Spieleentwicklung gedacht ist. Daher bietet es einige Funktionen, mit denen eine einfache Oberfläche erstellt werden kann. Hier zeigte sich eines der größten Probleme, die bei der Programmierung aufkamen. Geplant war es, kurze Videosequenzen als Übergänge oder im Hintergrund, um die Benutzeroberfläche etwas zu beleben. Nach einiger Recherche stellte sich allerdings heraus, das Pygame keine Möglichkeit bietet, Videos abzuspielen. Daher haben wir uns als Alternative überlegt, die einzelnen Bilder, aus denen ein Video besteht, einzeln abzuspeichern und nacheinander abzuspielen. Allerdings bedeutete dies auch, dass jedes Bild einzeln geladen werden muss, um dann angezeigt zu werden. Dies hat auch noch zuerst auf dem Computer funktioniert, allerdings stellte sich heraus, dass der Raspberry Pi mit dieser Aufgabe schlicht überfordert war. Zum einen ist er nicht schnell genug, um die Bilder in hoher Auflösung abzuspielen, zum anderen reichte der Arbeitsspeicher nicht aus, um überhaupt alle Bilder zu laden. Das erste Problem konnte leicht gelöst werden, indem wir die Auflösung der Bilder verringerten, allerdings tauchte das Problem wieder auf, wenn weitere Schaltflächen eingeblendet werden sollten. Das zweite Problem bestand auch noch weiterhin, und sämtliche Lösungsansätze funktionierten nicht ganz und waren nicht wirklich zufriedenstellend. Schließlich fand sich doch noch ein Weg mit „OpenCV“, ein Modul, das in erster Linie zur Bearbeitung und Analyse von Bildern gedacht ist. Dieses Modul ist jedoch auch dazu in der Lage, Videodateien abzuspielen, und lässt sich auch in Pygame einbinden. Nach ein paar Stunden herumprobieren und Troubleshooting war die Videowiedergabe im Programm eingebaut und konnte genutzt werden. Die Geschwindigkeit des Raspberry Pis ist zwar immer noch begrenzt, weshalb wir jetzt bei einer Bildschirmauflösung von 800x600 Pixeln sind. Diese Datei beinhaltet allerdings neben der Videowiedergabe noch weitere Werkzeuge. Dazu gehören einfache Bilder, auswählbare Schaltflächen, Textflächen mit automatischem Umbruch und eine Art Füllstandsanzeige, die beim freien Mischen das eingestellte Verhältnis anzeigt.
- ext_ui_methods.py: In dieser Datei befinden sich die Funktionen von den einzelnen Menüs, welche über paamestia.py aufgerufen werden. Der Aufbau dieser Funktionen ist etwas komplizierter geworden und könnte vereinfacht werden. Allerdings wäre dies durch den fortgeschrittenen Entwicklungsstand und den dafür
nötigen weitreichenden Änderungen sehr aufwendig und
durch das nahende Projektende nicht mehr umsetzbar. Im Folgendem wird einmal der Aufbau von einer der Funktionen gezeigt. Es handelt sich hierbei um den ersten Teil der Einstellungen, in denen zwischen den Optionen gewählt werden kann: Als erstes werden die benötigten
Variablen definiert. Dies
beinhaltet den Hintergrund und

sämtliche Bedienelemente und eine Variable, die anzeigt, dass das spezifische Menü aktiv ist, also angezeigt wird. Diese Variablen müssen global sein, damit ihr Zustand nicht verloren geht, wenn die Funktion wieder verlassen wird.

sc_active = False

sc_background = None | # background
sc_btns = [] | # list of all buttons
sc_pos = 0 | # positon / selected button

Als nächstes kommt die tatsächliche Funktion. Eingeleitet wird sie mit „global“. Dieser Befehl gibt an, welche Variablen schon global existieren und nicht neu lokal erstellt werden müssen. Dies ist wegen Pythons standardmäßigen Verhalten notwendig. Innerhalb einer Funktion werden Variablen immer zuerst neu erstellt, und nicht die schon vorhandene globale Variable geändert.

Abbildung 25: erste Ebene der Einstellungen

def settings_choose():

global sc_active, sc_background, sc_btns, sc_pos

Dann wird das erstmalige Aufrufen der Funktion abgehandelt. Erreicht wir dies, indem sc_active überprüft wird. Wenn diese Variable noch „Falsch“ enthält, dann wird diese Funktion zum ersten Mal aufgerufen. Ist dies der Fall, werden zuerst sämtliche Variablen definiert. Das wird erst beim Aufruf der Funktion gemacht, weil gerade die Oberflächenelemente viel Arbeitsspeicher benötigen. Würden alle Elemente direkt geladen werden, wäre der Arbeitsspeicher vermutlich wieder überlastet, daher werden diese Elemente nur gespeichert, wenn sie auch benötigt werden.

if sc_active == False: # when entering settings_choose

sc_active = True

sc_background = media_lib.Video(gl.gen_path + "/src/media/intro/intro.mp4") # create background

sc_background.start(repeat=True)

# create buttons

sc_btns.append(media_lib.Button(gl.gen_path + "/src/props/", "prop_white.png", "prop_green.png" , "prop_grey.png", 35, 35, 300, 530))

sc_btns[-1].add_text("Getränke", gl.debug_font, (0,0,255))

sc_btns.append(media_lib.Button(gl.gen_path + "/src/props/", "prop_white.png", "prop_green.png" , "prop_grey.png", gl.W-35-300, 35, 300, 530))

sc_btns[-1].add_text("Importieren", gl.debug_font, (0,0,255))

sc_btns[sc_pos].selected = True

Als nächstes überprüft das Programm auf eine Eingabe des Benutzers. Dazu wird die Datei io_lib.py verwendet, indem sie wie ein Python-Modul importiert wird. Hier wird bei der Eingabe überprüft, ob der Benutzer zurück zum Hauptmenü gehen möchte, oder welche der Einstellungen er auswählt.

# input

if io.read_input(io.BACK): | # if going back

sc_active = False

gl.prog_pos = 'm'

elif io.read_input(io.NEXT): | # selecting a setting

sc_active = False

if sc_pos == 0:

gl.prog_pos = 'sd'

else:

gl.prog_pos = 'si'

elif io.read_input(io.LEFT): | # moving the selection

sc_pos = 0

sc_btns[0].selected = True

sc_btns[1].selected = False

elif io.read_input(io.RIGHT):

sc_pos = 1

sc_btns[0].selected = False

sc_btns[1].selected = True

Schließlich werden die einzelnen Elemente „gezeichnet“, sprich auf dem Monitor angezeigt. Dabei ist die genaue Reihenfolge natürlich wichtig, damit nichts überdeckt wird .

# draw

sc_background.draw()

for i in sc_btns:

i.draw()

Zu allerletzt wird überprüft, ob diese Oberfläche wieder verlassen wird. Dazu wird überprüft, ob sc_active im Verlauf der Funktion wieder auf „Falsch“ gesetzt wurde. Wenn dies der Fall ist, werden alle Variablen, die viel Arbeitsspeicher benötigen wieder auf „None“ zurückgesetzt oder, wenn es sich um eine Liste handelt, wieder geleert.

if sc_active == False: # when leaving settings_choose

sc_background = None

sc_btns.clear()

- io_lib.py beinhaltet alle Funktionen für den In- und Output. Dieses Skript ist dementsprechend in zwei Teile aufgeteilt, einmal der Input und einmal der Output. Für den Input werden mehrere Funktionen benötigt. Zuerst sind da „keyboard_input()“ und „update_input()“, welche wiederholt aufgerufen werden müssen. Diese

Funktionen überprüfen einerseits, ob Tasten auf einer Tastatur gedrückt worden sind, und andererseits, ob die Taster an den GPIO-Pins betätigt worden sind. Um einen Tastendruck zu erkennen, wird für die Tastatur wieder das Pygame-Modul und für die Taster an den GPIO-Pins das Modul „gpiozero“ verwendet.

# read current state

if gl.os_is_linux: | # for the raspberry pi / but-
tons on gpio
up_state | = not UP_BT.is_pressed | # read every i
nput

down_state = not DOWN_BT.is_pressed

left_state = not LEFT_BT.is_pressed

right_state = not RIGHT_BT.is_pressed

next_state = not NEXT_BT.is_pressed

back_state = not BACK_BT.is_pressed

Diese Daten werden dann abgespeichert, und können, wann immer nötig über die Funktion „read_input()“ abgerufen werden. Hier ist außerdem eine kleine Besonderheit eingebaut: Es wird nicht gespeichert, ob eine der Taste gerade gedrückt wird, sondern nur, ob die Taste jetzt gerade betätigt wurde. Dabei steht „True“ für „Taster wird betätigt“ und „False“ für „Taster wird nicht betätigt“. Wenn jetzt eine Taste gedrückt wird, gibt es einen kurzen Impuls, in dem „True“ abgespeichert und das Programm wechselt wieder auf „False“, selbst wenn der Taster weiter gehalten wird.

def read_input(input):

""" returns input state as bool

input: key [UP, DOWN, LEFT, RIGHT, NEXT, BACK]

"""

global UP, DOWN, LEFT, RIGHT, NEXT, BACK

global up_state, down_state, left_state, right_state, next_sta te, back_state

global up_state_prev, down_state_prev, left_state_prev, right_ state_prev, next_state_prev, back_state_prev

# list of possible inputs and matching states

keys = [(UP, up_state, up_state_prev),

(DOWN, down_state, down_state_prev),

(LEFT, left_state, left_state_prev),

(RIGHT, right_state, right_state_prev),

(NEXT, next_state, next_state_prev),

(BACK, back_state, back_state_prev)]

is_pressed = False | # this varia-
ble will be set True when asked button is pressed. Otherwise it won't change
for key in keys: | # loops through key list

if key[0] == input and key[2] == False: # if tested key equals input and requested key is pressed

is_pressed = key[1] | # set is_press
ed = True

return is_pressed

Das Schalten der Ausgänge am Raspberry Pi gestaltet sich deutlich einfacher. Auch hier haben wir auf das „gpiozero“-Modul zurückgegriffen. Um einen Ausgangswert zu ändern muss nur die Funktion „write_output()“ verwendet werden.
- drink_lib.py kontrolliert alles was die Getränke, bzw. die Rezepte betrifft. Dieses Skript beginnt mit einer kleinen Setup-Routine, in der alle Getränke und Rezepte geladen werden. Dazu kann eingestellt werden, welche Getränke gerade an der Maschine angeschlossen sind und Daten abgerufen werden, zum Beispiel welche Rezepte gerade verfügbar sind.

""" ### SETUP ### """

# this part will run once, as soon this file is imported somewhere

# look for drinks

file1 = open(gl.gen_path + "/src/drinks", 'r') | # open file

drinks = file1.read-
lines() | # save lines as a list

file1.close()

for idx, i in enumerate(drinks): | # re-
move trailing newline characters

if drinks[idx].endswith('\n'):

drinks[idx] = drinks[idx][:-1]

print("[DR setup] drink list content:")

print(drinks)

# look for recipes

for filename in os.listdir(dir_recipes):

recipes.append(filename)

recipes.remove('free_mixed_reci-
pe') | # sort the free mixed recipe, as it should not ap-
pear in the recipe list

# sort lists

if gl.os_is_linux:

drinks.sort()

recipes.sort()

Die Rezepte werden in einem eigenen Ordner abgespeichert (Mehr dazu bei Punkt 5.10). Wird nun ein Rezept ausgewählt, dann wird es geladen und in selbst entwickelte Befehle übersetzt. Die Syntax der Befehle ist sehr simpel, und es gibt nur eine begrenzte Anzahl von Befehlen. Das erste Zeichen eines Befehls gibt an, was getan werden soll, bzw. um was für einen Befehl es sich handelt. Die restlichen Zeichen bilden den dazugehörigen Parameter. Hier eine Auflistung der Befehle und deren Funktion:
Befehl | Funktion | Beispiel
o<Ventil> | Ventil öffnen und Pumpe starten | „o3“ öffnet das dritte Ventil und startet die Pumpe
c<Ventil> | Ventil schließen und Pumpe stoppen | „c1“ schließt das erste Ventil und stoppt die Pumpe
t<Ventil> | Stellt eine Stoppuhr ein (Zeit in Millisekunden) | „t4200“ stellt die Stoppuhr auf 4.2 Sekunden
w | Warten, bis die Stoppuhr ab-gelaufen ist. Dieser Befehl folgt immer auf „t“ | Das Programm misst die vergange-nen Sekunden und geht erst zu dem

| | nächsten Schritt über, wenn die 4.2 Sekunden verstrichen sind
e | Dieser Befehl signalisiert, dass das Rezept abgeschlos-sen ist, und beendet damit den Vorgang

Hier ein kurzes Beispiel von einem kompilierten Rezept:

o1 | # erstes Ventil öffnen
t3000 | # Timer auf 3 Sekunden stellen
w | # Auf Ablauf des Timers warten
c1 | # erstes Ventil schließen

o4 | # viertes Ventil öffnen
t12000 | # Timer auf 12 Sekunden stellen
w | # Auf Ablauf des Timers warten
c4 | # viertes Ventil schließen
e | # Mischprozedur beenden

Diese Befehle werden dann während der Mischprozedur ausgeführt. Eine Variable zählt dabei den aktuellen Arbeitsschritt mit, indem sie nach jedem abgeschlossenen Arbeitsschritt um eins erhöht wird.

def update_mixing():

global is_mixing, recipe_step, commands, finishing_time

if is_mixing: | # if something is currently mixed

cmd = commands[recipe_step]

if cmd[0] == 'o': | # open valve

valve = int(cmd[1])

print("[DR UM] open valve " + str(valve))

io.write_output(io.VALVES[valve], 1)

io.write_output(io.PUMP, 1)

recipe_step += 1

elif cmd[0] == 'c': | # close valve

valve = int(cmd[1])

print("[DR UM] close valve " + str(valve))

io.write_output(io.VALVES[valve], 0)

io.write_output(io.PUMP, 0)

recipe_step += 1

elif cmd[0] == 't': | # set timer

print("[DR UM] set timer " + cmd[1:] + " ms")

finishing_time = current_milli_time() + int(cmd[1:])

recipe_step += 1

elif cmd[0] == 'w': | # wait

t = current_milli_time()

if t >= finish-
ing_time: | # if waited long enough, advance to next step

recipe_step += 1

elif cmd[0] == 'e': | # end sign
print("[DR UM] end mixing") | # stops the mixing pro-
cess

is_mixing = False

# add debug information

if gl.show_debug:

gl.debug_text.append("MIX cur. cmd.: " + str(cmd) + "; prev. cmd.: " + str(commands[recipe_step-1]))

gl.debug_text.append("MIX cmd nr.: " + str(recipe_step) + " / " + str(len(commands)))

5.9.3. DATEIEN UND RESSOURCEN FÜR DIE SOFTWARE

Unser Programm benötigt einige Dateien für die grafische Oberfläche und die Rezepte. Diese Dateien befinden sich alle im „src“-Ordner. Wir werden hier einen kurzen Überblick über die verschiedenen Dateien geben:

- Ordner „fonts“: Hier sind die Fonts, also Schriftarten abgespeichert.
- Ordner „media“: Hier drin befinden sich alle Videos und Bilder für die Benutzeroberfläche. Wir bauen die Oberfläche in erster Linie aus einigen Bilder auf, die jeweils einzelne Elemente der Benutzeroberfläche darstellen. Beispielsweise wird die Rezeptauswahl aus zwei Bildern erstellt: Abbildung 27 zeigt die ausgewählte Schaltfläche, Abbildung 26 eine normale Schaltfläche. Daraus wird eine komplette Liste erstellt, wie in Abbildung 28 zu sehen ist.
- Ordner „recipes“: In diesem Ordner sind alle Rezepte, die Importierten miteingeschlossen, abgespeichert. Die Rezepte sind einfache Textdateien und beschreiben, welche Getränke in welcher
Menge benötigt werden. Diese Dateien

werden gelesen, und zum Beispiel bei der Rezeptauswahl aufgelistet. Ausnahme ist hierbei die Datei „free_mixed_recipe“, welche das Mischverhältnis beim freien Mischen zwischenspeichert.
- Dateien „drinks“ und „drinks_custom“: In diesen beiden Dateien werden die verfügbaren Getränke abgespeichert. „drinks“ beinhaltet dabei eine vorgefertigte Liste, in „drinks_custom“ werden zusätzliche Getränke abgespeichert.
- Datei „.windows“: Diese Datei wurde zu Entwicklungszwecken erstellt. Anhand dieser Datei erkennt das Programm, ob es auf einem PC oder dem Raspberry Pi ausgeführt wird. Dies ist notwendig, weil das Programm während des Entwickelns auf einem Windows-PC ausgeführt wurde, im fertigen Projekt aber auf einem Raspberry Pi mit Linux. Ob das Programm in Windows oder in Linux ausgeführt wird, wird in der Variable „os_is_linux“ (in „globals.py“) gespeichert. Wenn ein Befehl ausgeführt wird, der nur auf dem Raspberry Pi ausgeführt werden kann, wird erst mittels dieser Variable das System überprüft. Auf diese Weise kann es zum Beispiel nicht passieren, dass das Programm versucht ein Magnetventil am PC anzusteuern.

Abbildung 27: ausgewählte Schaltfläche

Abbildung 26: normale Schaltfläche

Abbildung 28: fertige Benutzeroberfläche

5.10. ENTWICKLUNG DER BENUTZEROBERFLÄCHE
5.10.3. VORWORT

Die Benutzeroberfläche hat, im Laufe des Projektes, mehrfach drastische Entwicklungen durchlaufen, jedoch im Kern immer die gleiche Idee verfolgt. Die Software, die zur Erstellung dieser Benutzeroberfläche benutzt wurde, behandelt ein für viele Menschen unbekanntes Thema was zur Folge hat, dass der Großteil der Leser dieser Dokumentation das Folgende Kapitel nur teilweise oder kaum verstehen können. Um dies vorzubeugen, folgt nach diesem Vorwort ein Glossar, was die wichtigsten Begriffe rund um das Themenfeld 3D-Modeling und Rendering erklärt.

Modulnummer | 7
Modulname | Entwicklung der Benutzeroberfläche
Ziel des Moduls | Entwerfung und Entwick-lung einer
Veranschlagte Zeit | So viel wie nötig / Heim-arbeit | Benötigte Zeit | 300h
Mitwirkende | Dominic Kosin

## Benutzte Software

Blender | Krita
Zbrush | Substance Designer
Maya | Inkscape

5.10.4. BENUTZEROBERFLÄCHE

Grundlagen des 3D-Modelings

Software, die für das Themengebiet des 3D-Modelings entwickelt wurde, hat immer den gleichen Grundgedanken. Nämlich die Darstellung, Erzeugung und Manipulation von Objekten (Primitive) im 3-dimensionalen Raum. Diese Objekte können nur ein Einzelner Punkt (Vertex Mehrzahl Vertecies), eine zweidimensionale Linie (Edge) oder ein Dreidimensionales Objekt (Polygon) sein. Diese Objekte können dann mit den Software-spezifischen Funktionen manipuliert werden, um jedes beliebige Objekt zu erschaffen. Zwei Vertecies bilden eine Edge und mindestens 3 miteinander verbundene Edges ergeben ein Polygon. In der Industrie werden heutzutage nur Dreieckige, Viereckige und Fünfeckige Polygone benutzt. Man Unterscheidet grundsätzlich unter zwei Arten des 3D-Modelings. Das ,,Hard-Surface-Modeling" und das ,,Sculpting”. Beide Methoden haben ihre Vor- und Nachteile und somit auch spezifische Anwendungsbereiche. ,,Hard-Surface-Modeling" wird dann verwendet, wenn man ein Objekt erstellen will, was nicht organisch ist wie z. B. ein Haus, ein Stuhl oder eine Brieftasche. Dabei manipuliert man Vertecies, Edges und Polygone, um seine gewünschte Form zu bekommen. Das Sculpting hingegen wird für das Erstellen von organischen Objekten gebraucht. Sie können sich dies als virtuelles Tonformen vorstellen, wo der Künstler mit verschiedenen Werkzeugen die Vertecies, Edges und Polygone manipuliert, bis die gewünschte Form entsteht.

Wireframe (Gitternetz)

Das Wireframe wird durch die unterschiedlich verbundenen Vertecies, Edges und Polygone gebildet, die so die Oberfläche des Objektes darstellen. Es ist sehr wichtig, während der Erstellung von 3D Objekten, ein für den Verwendungszweck passendes Wireframe zu erstellen, um später beim Weiterverarbeiten des Objektes nicht auf Komplikationen zu stoßen. Dies wird in den meisten Fällen durch konsequente und saubere Arbeit geregelt, und erfordert deswegen aber auch Planung, Geduld, Übung und sehr viel Zeit.

UV-Mapping

UV-Maps werden erstellt, um Objekte mit einer Textur zu versehen. Diese Maps sind zweidimensionale Bilder, die die Position der Vertecies, Edges und Polygone speichert. Eine Besonderheit dieser UV-Maps ist auch die Eigenschaft, die Tiefe der einzelnen Polygone, Edges und Vertecies zu speichern. UV-Maps werden in der Regel durch das Setzen von sogenannte ,,Cuts” und das Aufklappen des 3D-Models erstellt. Eine einfache bildliche Erklärung wäre das Sie einen 3-dimensionalen 6-seitigen Würfel flach auf ein Blatt Papier legen wollen. Dazu schneiden Sie die Kanten an dem Würfel auseinander, bis dieser mit allen 6 Seiten flach auf der zweidimensionalen Fläche liegt.

Node-Based Programming

Ein Großteil der jetzigen Software, die mit 3-dimensionalen Objekten zu tun hat, benutzt für die Manipulierung und auch die Shader Erstellung sogenannte ,,Nodes”. Jede Node hat ihre eigene Funktion und Anwendungsbereich. Diese Art des Programmierens wird auch als flussbasiertes Programmieren bezeichnet.

Physically Based Rendering

Pysically Based Rendering, kurz PBR, ist eine computergrafische Herangehensweise, Modelle fotorealistisch darzustellen. Diese Technik umfasst das Erstellen von bestimmten Texture-Maps, die gewisse Informationen zur Fotorealistischen Berechnung von Physikalischen Eigenschaften enthalten.

High Dynamic Range Images

Kurz HDRIs versteht man verschiedene Techniken zur Aufnahme und Wiedergabe von Bildern mit großen Helligkeitsunterschieden ab etwa 1:1000. Diese werden zur Realistischen Beleuchtung von 3-dimensionalen Szenen benutzt, wo jeder Pixel in Abhängigkeit seiner Helligkeit einen Lichtstrahl auf die 3D- Szene projiziert.

Path Traced Rendering

Beschreibt einen Algorithmus zur Bildsynthese, der die Simulation der globalen Beleuchtung ermöglicht. Dies erfolgt durch rigorose mathematische Verfahren, die Strahlen in die Szene schicken. Diese Strahlen werden dann entweder reflektiert, gebrochen oder absorbiert, wobei jedes Mal ein zufälliger Strahl generiert wird. Die auftretenden Fehler werden als Varianz oder Bildrauschen dargestellt. Diese Varianz wird auch Noise genannt.

Postprocessing

Postprocessing beschreibt die Weiterbearbeitung und Aufbereitung von computergenerierten, synthetischen Bildern.

5.10.5. BENUTZTE SOFTWARE

Die benutzte Software muss zum größten Teil selbst finanziert werden. Die Wahl fiel auf diese Software, da so ein Reibungsloser und Komplikationsfreier Workflow gewährleistet war. Es wurde die Software ,,Blender” und die integrierte Renderengine Cicles, Maya, die Renderengine Arnold, Substance Designer, Krita, Inkscape, Zbrush, und Pixlr verwendet. Davon waren Maya und Blender und Zbrush die hauptsächlichen Programme zum Erstellen und Rendern der 3D-Modelle. Krita, Inkscape und Pixlr wurden zum Bearbeiten und Erstellen von Zeichnungen und Bildern genutzt. Substance Designer ist hauptsächlich nur zum Erstellen von PBR-Texturen nützlich.

5.10.6. WORKFLOW

Durch die diverse Menge an unterschiedlichen Programmen, die zur Erstellung der Benutzer Oberfläche verwendet wurden, war eine Einteilung der Programme nötig, um den effizientesten Weg zur Fertigstellung zu finden. Der Workflow setzte sich aus den verschiedenen Schwächen und Stärken der jeweiligen Programme zusammen. Ein weiterer Faktor für die Zusammensetzung war die eigene Erfahrung im Umgang mit den Programmen. Der persönliche Stand vor dem Start des Projektes lag bei der fortgeschrittenen Nutzung der Programme Blender, Inkscape, Pixlr, Zbrush und Krita. Im Laufe des Projektes wurden diese Fertigkeiten vertieft, und den Umgang mit den Programmen Maya und Substance Designer selbstständig erlernt.

5.10.7. FEHLGESCHLAGENE VERSUCHE UND UNBENUTZTE OBJEKTE
5.10.7.1. GRUNDLEGENDE IDEE

Die Grundlegende Idee dieser Benutzeroberfläche war es, ein Menü bestehend aus verschiedenen Bereichen zu erstellen. Diese Bereiche hätten dann eine bestimmte Funktion, die dem Kunden die Maschine bedienen lassen würde. Diese Idee ging noch weiter, denn da unsere Maschine einer Bar nachempfunden wurde, sollten die verschiedenen Bereiche von einem virtuellen Barkeeper, der in einer Bar arbeitet, begleitet werden, so wie auch Übergänge einleiten und den Kunden die Wartezeit mit Witzen verkürzen sollte. Der Hintergedanke war so die Benutzung der Maschine menschlicher und persönlicher zu gestalten. Die Funktion und der Inhalt dieser Bereiche wurden schon nach der Festlegung des Projekt-Themas aufgegriffen und bestimmt.

5.11.7.2. DIE VIRTUELLE BAR PAAMESTIA

Diese Version erstellte ich daraufhin in dem Zeitraum der kompletten Winterferien 2020 und ein paar Wochen stückweise danach. Schätzungsweise verwendete ich, bis zu dem Stand der letzten Änderung, 200 Stunden nur mit dem Designen und Erstellen der 3D-Modelle für die begleitenden Videos des Paamestia-Automaten. Die Vorgehensweise, die ich beim Designen und Erstellen dieser Version gewählt habe, war rückblickend sehr ineffizient und langsam. Des Weiteren habe ich die meisten Ideen für das Design während des Erstellens anderer Objekte und im Schlaf bekommen. Dies verlangsamte den Erstellungsprozess immens, denn durch die nicht grobe Festlegung eines Designs durchliefen fast alle Modelle mehrere Iterationen, wo diese Modelle, von Grund auf, neu entwickelt worden. Der Workflow für diese Modelle war immer der gleiche. Die Haupterstellung wurde in dem Programm Blender gemacht, da ich mit diesem Programm die meiste Erfahrung hatte. Trotz dessen musste ich bei Modifikationen, um das gewünschte Objekt zu kreieren, auf das Modeling spezialisierte Programm Zbrush zurückgreifen, da dieses mit Problemen klarkommt, wo das Programm Blender Fehler aufweist. Insgesamt besteht die komplette Szene aus 278 Modellen. Um sich etwas von solchen Ausmaßen auszudenken zu können, muss man sich im Klaren sein was sein Endprodukt sein sollte. Deshalb bereitete ich ein Szenario vor, wo diese Bar spielen sollte, und schrieb dazu eine Geschichte, die diese Bar glaubwürdiger machen sollte. Die Bar selbst würde in einem Gebäude stehen, was gleichzeitig ein Treffpunkt für allerlei Menschen mit unterschiedlichen Hobbys ist. Merkmale sollten die Bücherei, die Zentrierte Bar, die Bühne, Form und Architektur sein. Die Haupt-Inspiration war die Viktorianische und Anthroposophische Architektur.

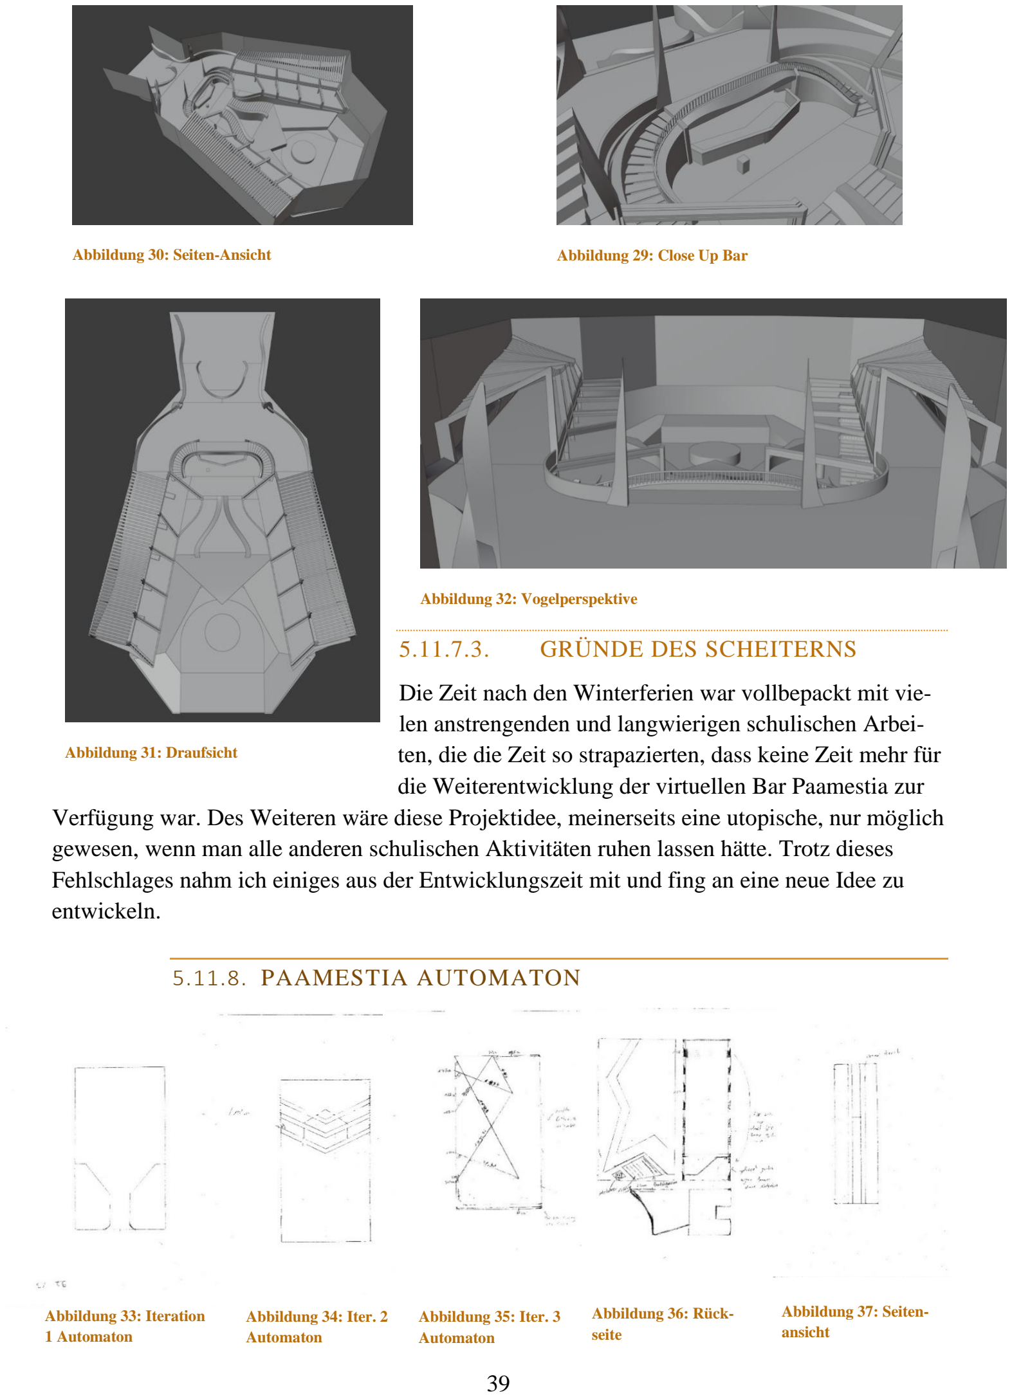
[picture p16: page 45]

5.11.7.3. GRÜNDE DES SCHEITERNS

Die Zeit nach den Winterferien war vollbepackt mit vielen anstrengenden und langwierigen schulischen Arbeiten, die die Zeit so strapazierten, dass keine Zeit mehr für die Weiterentwicklung der virtuellen Bar Paamestia zur Verfügung war. Des Weiteren wäre diese Projektidee, meinerseits eine utopische, nur möglich gewesen, wenn man alle anderen schulischen Aktivitäten ruhen lassen hätte. Trotz dieses Fehlschlages nahm ich einiges aus der Entwicklungszeit mit und fing an eine neue Idee zu entwickeln.

5.11.8. PAAMESTIA AUTOMATON
Abbildung 30: Seiten-Ansicht | Abbildung 29: Close Up Bar

Abbildung 31: Draufsicht

Abbildung 32: Vogelperspektive

Abbildung 33: Iteration

### 1 Automaton

Abbildung 34: Iter. 2
Automaton

Abbildung 35: Iter. 3
Automaton

Abbildung 36: Rückseite

Abbildung 37: Seitenansicht

Die alte Idee wurde verworfen und ich entwickelte eine neue Idee. Diesmal war die eigentliche Benutzeroberfläche im Vordergrund. Daher sollte die Auswahl eher an einen Getränkeautomaten erinnern. Die Idee war, das beim Auswählen des gewünschten Rezeptes eine Animation abspielen würde, die dem Kunden das Getränk visuell erklärt und schmackhaft macht. Des Weiteren sollten beim Bereich ,,Import Recipe” der eigentliche Automat zu sehen sein und in dem Bereich ,,Select Drinks” die Getränkesorte durch Farben und gegebenenfalls Früchten visualisieren. Ich fing diesmal anders an, und entwarf erste Konzepte für den Automaten, dem Herzstück des Programmes. Nach einigen Iterationen fand ich das richtige Design und verfeinerte es, bis es fertig zum Modellieren war.

Das Model wurde diesmal zum größten Teil in dem Programm Zbrush entwickelt, da ich durch die virtuelle Bar Paamestia meine Fähigkeiten in diesem Programm stärken konnte. Das Grundgerüst wurde jedoch in dem Programm Blender erstellt. Dort habe ich dann einfach Vertecies an den Punkten, die ich in dem Entwurf niedergeschrieben habe, platziert, verbunden und zu einem Objekt zusammengefügt. Ich hielt mich strickt an meinen Entwurf und setzte ihn genauso um. Zwischendurch musste das Objekt optimiert werden, da es angedacht war dieses Objekt zu Texturieren. Ich entschied mich dafür, das Objekt in einem Wireframe zu erstellen, welches komplett aus Vierecken besteht, da das Model eine sehr komplexe Struktur aufweist. Nach etwa 50 Stunden war das Model
komplett fertig und bereit zum Texturieren. Doch
zuvor musste das Modell UV-Unwrapped werden.
Meine Entscheidung, das Wireframe komplett aus Vierecken zu machen und die Arbeit, das Modell zu optimieren, zeigten sich hier als sehr nützlich. Das UV-Unwrapping wurde in dem Programm Maya vollzogen, da es sehr hilfreiche Funktionen für diesen Bereich zur Verfügung stellt.

Gründe des Scheiterns

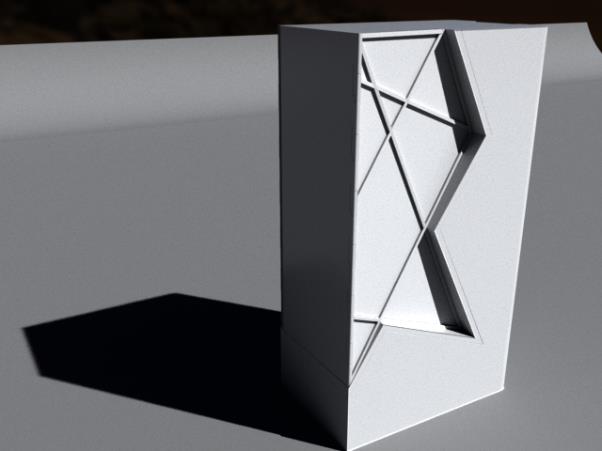
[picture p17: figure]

Nach Fertigstellung des Modelles und Beendigung der Vorbereitung zum Texturieren wurde die Menge an zu erledigenden Hausarbeiten für bestimmte Fachrichtungen so massiv, dass wieder keine Zeit für die weitere Entwicklung des Projektes übrig war. Als sich dies jedoch wieder legte, war die übrige Zeit bis zur Abgabe sehr begrenzt und ich entschied mich dazu, diese Stelle ruhen zu lassen, bis die Benutzeroberfläche fertig ist.

Abbildung 38: Automaton Render

Abbildung 39: UV-Map 1 | Abbildung 40: UV-Map 2 | Abbildung 41: UV-Map 3 | Abbildung 42: UV-Map 4

5.11.9. BENUTZEROBERFLÄCHE

Logo

Die generelle Idee, wie das Logo aussehen sollte stand schon seit langem fest. Nämlich seit der virtuellen Bar „Paamestia“. Während dieser Zeit entwickelte ich ein Logo und erstellte sogar schon eine ,,Titelbild”-Szene. Es sollte eine Art Blume sein, die uns und unser Bestreben, in irgendeiner Weise, repräsentiert. Nach dem ich den Paamestia Automaten habe ruhen lassen, machte ich mich an die Entwicklung eines Logos. Dies zeichnete ich in dem Programm Krita, mehrere Male in verschiedenen Ausführungen, bis ich
zufrieden mit dem Design war. Um das Design zu optimieren,
zeichnete ich die vorgemalten Linien mit einem gewichteten
Stift nach, der die Linien konstant bleiben lässt. Das fertige Bild importierte ich dann in das Programm Inkscape, wo ich es weiterverarbeite damit ich es in einem 3D-Programm verwenden kann. In Inkscape verwendete ich eine Funktion, die die Bitmap eines Schwarz-Weiß-Bildes nachzeichnet und so eine SVG-Datei erstellt. Diese Datei kann ich dann in Maya importieren, um dort die Szene für das Rendern (Bildsynthese) vorzubereiten.

Sequence

Nachdem das Logo fertig war, begann ich eine Startsequenz zu animieren. Es sollte eine Hommage an den gedachten Automaten sein, also war die Idee ein Computer-Boot zu animieren. Die fertige Animation war in zwei getrennt gemachte Sequenzen geteilt, die beide in 24 Frames die Sekunde laufen. Zuerst der Computer-Boot und dann die Ladeanimation. Glücklicherweise stellte ich fest, dass das Logo selbst ein interessantes Ladezeichen ergeben würde, also nahm ich das fertige Logo auch dafür. Den Ladebalken erstellte ich aus einem Quadrat, wo ich die Ecken abrundete, die vorderste und hinterste Fläche modifizierte und schließlich löschte. Das Logo und dem Ladebalken gab ich einem programminternen PBR-Shader, den ich durch gezielte Einstellungen weiß und reflektiv gestaltete. Zusätzlich zu dem Shader platzierte ich 6 unterschiedlich starke ,,Area Lights” die die Modelle beleuchten sollten. Die Kamera stellte ich auf die gewünschte Größe des Bildes und platzierte sie so, dass alles im Bild ist und stellte die Länge der Animation in der Zeitlinie ein.

Für die Animation des Logos setzte ich Key-Frames an verschiedenen Punkten in der Zeitlinie. Die Animation des Logos beginnt erst ab dem 25. Frame und endet beim 144. Frame. Die Key-Frames wurden so periodisch gesetzt und eingestellt, dass das Logo sich 720 Grad in 23 Frames bewegt und dann dies nach 10 Frames wiederholt. Der Graph, der diese Bewegung darstellt, wurde so eingestellt, dass diese Bewegung nicht linear von statten geht.

Abbildung 43: Logo Paamestia

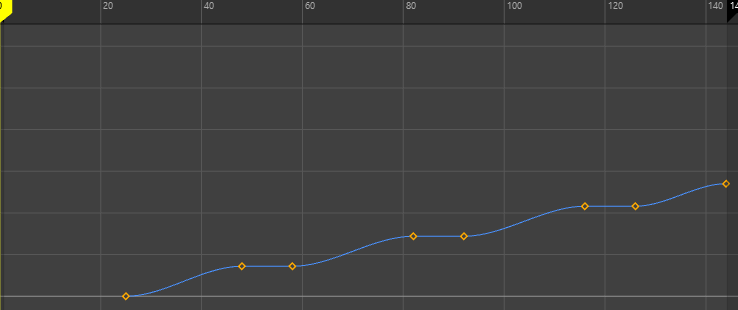
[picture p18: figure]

Das Model des Ladebalkens
wurde in 4 verschiedene Flächen aufgeteilt und so mit Key-Frames animiert, das diese Flächen zu einem bestimmten Zeitpunkt auf der Zeitlinie sichtbar für die Kamera werden. Für zusätzlichen Realismus wurde Motion-Blure
aktiviert, was den Shutter-Speed
von Digitalkameras simuliert.

Diese fertige Animation wurde dann in 144 verschiedenen Bilder gerendert und später in eine Video-Sequenz zusammengefügt.

Den Inhalt der Booting-Sequenz wurde
auf einen Zettel niedergeschrieben und
anschließend in einem 3D-Programm
in digitalen Text
konvertiert. Diese
wurden dann als

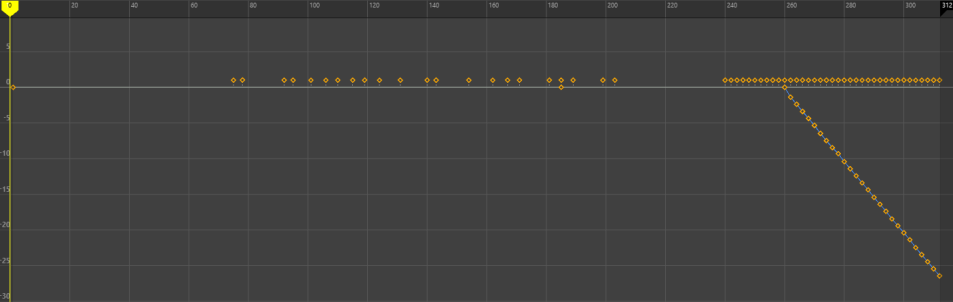
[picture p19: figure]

Zeilen zusammengefügt und in Maya importiert. Der PBR-Shader ist genau derselbe wie bei dem Ladebalken. Die Animation geht insgesamt 312 Frames. Der erste Teil der erstellten Animation beginnt ab dem Frame 75 und läuft bis zum Frame 203. In diesem Zeitraum tauchen in unregelmäßigen Abständen Buchstaben auf die den Satz ,,project paamestia:start”
ergeben. Dies soll das Gefühl vermitteln, das ein
Mensch diesen Befehl in die Maschine eingibt und In-

teresse wecken. Ab dem Frame 240 Tauchen dann, in periodischen Abständen die vorher festgelegten Linien auf. Ab dem Frame 260 kommt dann auch noch eine periodische Bewegung der Linien, um einen bestimmten Wert, um Scrollen zu simulieren. Diese beiden periodischen Ereignisse passieren alle zwei Frames einmal.

Diese Animation wird auch wieder in 312 Bildern gerendert.

Anschließend wurden beide Sequenzen in dem Videoschnittprogramm Shortcut zusammengefügt.

Komposition der Benutzeroberfläche

Wie diese Bereiche der Benutzeroberfläche nun genau aussehen sollten, konzipierte ich zuallererst, um mir einen groben Überblick über das gesamte Ausmaß zu verschaffen. Dieses

Abbildung 44: Keyframes Logo

Abbildung 45: Render Logo und Ladebalken

Abbildung 46: Keyframes Booting Sequence

Konzept war lediglich eine reine Gedankenstütze und kann nicht mit dem finalen Ergebnis gleichgesetzt werden.

Generelle Vorgehensweise zur Umsetzung des Designs

Alle Designs der Benutzeroberfläche, die jetzt folgen werden, wurden mit den gleichen Techniken erstellt. Die Konzepte wurden in dem Programm Krita erstellt und waren hier wieder nur eine Gedankenstütze und können nicht mit dem finalen Produkt gleichgestellt werden. Trotzdem wurden diese Konzepte für die Erstellung der Modelle gebraucht. Die meistgenutzte Technik, die zum Erstellen dieser Modelle gebraucht wurde, ist die des Platzierens von Vertecies an den vermeintlichen Positionen und diese dann zu einem Polygon zu verbinden. All die Details und Muster wurden mithilfe der ,,Inset”-Funktion und Boolean-Operatoren erstellt. Bei der Inset-Funktion werden die Edges eines Polygons kopiert und können beliebig in dem Polygon oder außerhalb platziert werden. Werden diese jedoch in dem Polygon platziert, wird das Polygon geteilt und es Entstehen weitere Edges. Diese können dann auch wieder mit verschiedenen Operatoren manipuliert werden, um das gewünschte Objekt zu bekommen. Die Boolean-Operation hingegen entfernt die geschnittene Fläche eines Operators mit einem anderen Objekt.

Schriftart

Die benutzte Schriftart auf der Benutzeroberfläche ist ,,Da Mad Rave” von Darell Flood. Diese wurde auf der Webseite Dafont.com heruntergeladen und ist für nicht kommerziellen Gebrauch kostenlos.

wichtigste Komponenten der Benutzeroberfläche

Im Grunde besteht die gesamte Benutzeroberfläche aus einem sich wiederholenden Muster von Grundformen, die ich während des Design-Prozesses entwickelt habe. Das generelle Aussehen dieser Flächen wurde von dem zuvor entwickelten Paamestia-Automaten stark beeinflusst. Zum Zweck der effizientesten Arbeitsmethode wurde oft die Form verschiedener Objekte wiederverwertet. Dies wird bei genauerer Betrachtung in dem Bereich der Listen deutlich. Dort wurde die ,,normale Fläche”, die Form der ,,ausgewählten Fläche” und den ,,Button” mehrfach in unterschiedlichen Aufmachungen genutzt. Diese unterschiedlichen Aufmachungen wurden, nach dem Fertigstellen der Grundform, durch reines Ausprobieren und Manipulieren erstellt.

Main Menu

Das Main Menu beinhaltet die essenziellen Flächen, die benötigt werden, um durch das Programm zu gelangen. Durch genauere Absprache mit unserem Programmierer Arvid Randow hatte ich die nötigen Informationen, wie die wirkliche Programmierung aussah und entwickelte daraufhin zugeschnittene Formen für diese Anwendung. Das fertige Design lässt dem Kunden diese vier verschiedenen Flächen ansteuern, was mit einem Farbwechsel der ausgewählten Flächen indiziert wird. Des Weiteren wurden die Flächen mit dem korrespondierenden Beschreibungstext versehen. Die gewählte Sprache für die Benutzeroberfläche war Englisch, aus dem einfachen Grund, dass diese Sprache kürzere Wörter für die Schlüsselwörter der Flächen enthält und so die Möglichkeit bereitstellte, eine größere Schriftgröße zu Verwenden.

Die Hauptfläche ,,Recipes”, anders als die anderen Flächen zu Designen, hatte den Hintergedanken, so diese Fläche von dem Rest abzuheben und bei dem Benutzer Interesse zu wecken.

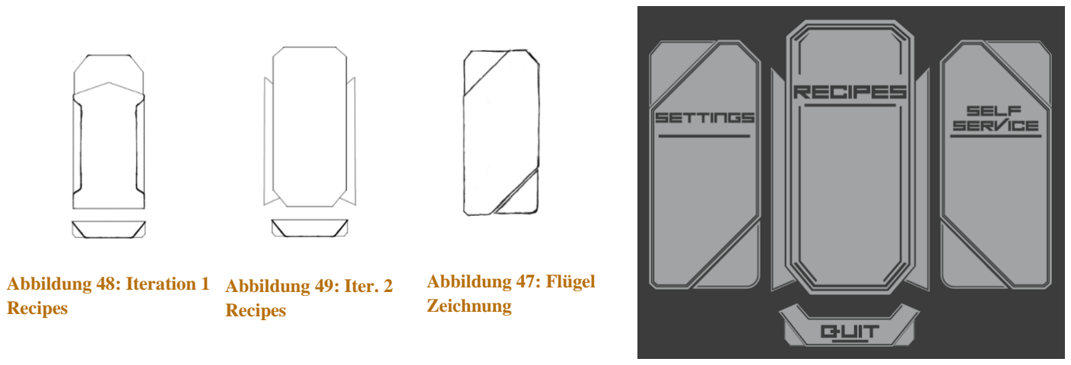
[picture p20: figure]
Abbildung 48: Iteration 1; Recipes; Abbildung 49: Iter. 2; Abbildung 47: Flügel; Zeichnung

Settings

Um Ressourcen und Zeit zu sparen, wurde hier die linke und rechte Fläche des Main Menus wiederverwendet. Einen weitgreifenden Hintergedanken bei dem Design gab es auch nicht, da der Bereich ,,Settings” nicht im Vordergrund lag. Der Kunde hat in diesem Bereich die Möglichkeit, in die weiteren Bereiche ,,Select Drinks” und ,,Import Recipes” zu kommen. Dies wurde wieder durch einen Farbwechsel der ausgewählten Fläche indiziert.

Select Drinks

Die Hauptaufgabe dieses Bereiches war die Festlegung der verwendeten Getränke, um die verschiedenen Rezepte, und auch den Bereich ,,Self Service” korrekt benutzen zu können. Ohne diese Festlegung würde das Programm die Fertigstellung der vorprogrammierten Rezepte nicht initiieren und den Bereich ,,Self Service” komplett unbrauchbar gestalten. Damit der Benutzer volle Kontrolle über das Festlegen, welche Getränke er in welchem Slot anschließt, verfügt, hat er die Möglichkeit, hier in diesem Bereich das benutzte Getränk in der von uns voreingestellten Liste zu suchen und es im Programm abzuspeichern. Der Slot kann durch Auswahl der Nummer rechts von der ursprünglichen Auswahl-Fläche geändert werden. Die ausgewählte Fläche wird auch hier wieder mit einem Farbwechsel indiziert, die Ausnahme hierbei stellen die Pfeile in den verschiedenen

Abbildung 50: fertige Ansicht Main Menu

Abbildung 51: fertige Ansicht Settings

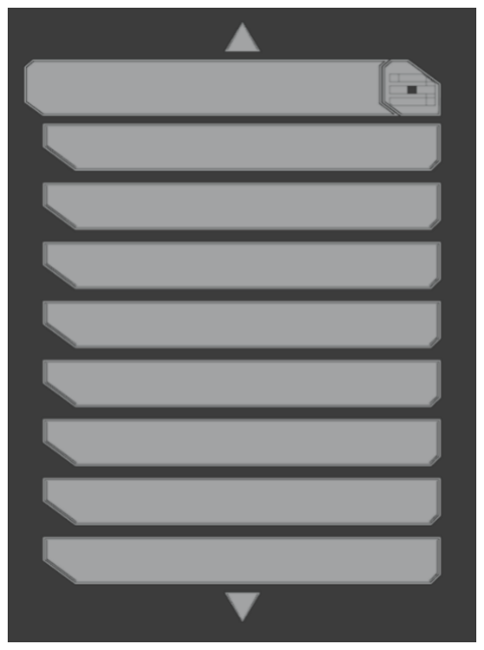
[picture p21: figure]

Abbildung 52: fertige Ansicht Select Drinks

Listen dar. Diese sind von Anfang an rot und werden erst grau, wenn diese das Ende der jeweiligen Seite der Liste erreicht hat.

Import Recipes

Zum Zweck der Erweiterung hat der Benutzer die Möglichkeit eigene Rezepte in die Maschine zu importieren. Dies wird in dem Bereich
,,Import Recipes” durchgeführt. Das Design was hier
für entwickelt wurde, besteht zum Teil aus den gleichen Flächen wie die Liste in dem Bereich ,,Select Drinks”. Der signifikante Unterschied hier ist die Positionierung dieser Listen, die Entfernung der Slot-Nummer und den neu eingefügten ,,Delete” und ,,Import” Buttons. Die ausgewählte Fläche wird hier auch wieder mit einem Farbwechsel indiziert. Der Kunde hat nur die Möglichkeit seine eigenen importierten Rezepte zu löschen. Die von uns festgelegten Rezepte sind fester Bestandteil der Maschine und dürfen nicht gelöscht werden.

Self Service

Da wir uns nicht nur auf die Herstellung von Getränken nach Rezepten spezialisieren wollten, kam uns die Idee, den Kunden die Möglichkeit zu geben, sich eigens die gewünschte Menge eines oder mehrerer angeschlossenen Getränke zubereiten zu lassen. Der Kunde hat in dem

Bereich ,,Self Service” die Möglichkeit, an den verschiedenen Slots das voreingestellte Getränk in 10%
Schritten, bis das vorgegebene Limit der 100% erreicht ist, einzustellen und auszuführen. Diese Prozentanzeige wird einmal mit Strichen in den korrespondierenden Slots und einer Nummer angezeigt. Die Slots werden hier als Türme dargestellt, die die gleiche Nummerierung wie die eingestellten Getränkeslots besitzen. Die ausgewählte Fläche wird hier wieder mit einem Farbwechsel indiziert.

Abbildung 53: fertige Ansicht Import Recipes

Abbildung 54: Iteration 1 Prozent Abbildung 55: Iter. 2 Prozent

Abbildung 56: fertige Ansicht Self Service

Recipes

Dies war der Bereich, der unsere Hauptidee eines Getränkeautomaten widerspiegelt. In dem Bereich ,,Recipes” hat der Kunde die Möglichkeit von einer von uns erstellten erweiterbaren Liste eine Vielzahl von unterschiedlichen Rezepten eins auszuwählen und diese von unserer Maschine mischen zu lassen. Hier wurde sich auch
wieder an dem ursprünglichen Listen-Design bedient
und leicht umgewandelt. Es wurde auch dieselbe Aufmachung wie beim Bereich ,,Import Recipe” verwendet, weil diese sich hierfür sehr gut geeignet hat. Besonderheit dieses Bereiches ist, dass die Rezepte erst funktionieren, wenn die für die Herstellung benötigten Getränke in dem Bereich ,,Select Drinks” eingestellt sind, um so eine falsche Benutzung zu verhindern. Des Weiteren erscheint ein Informationstext, sobald der Kunde Interesse an einem Rezept zeigt und dieses auswählt. Die Auswahl wird hier wieder mit einem Farbwechsel der ausgewählten Fläche indiziert.

Texturierung der Benutzeroberfläche

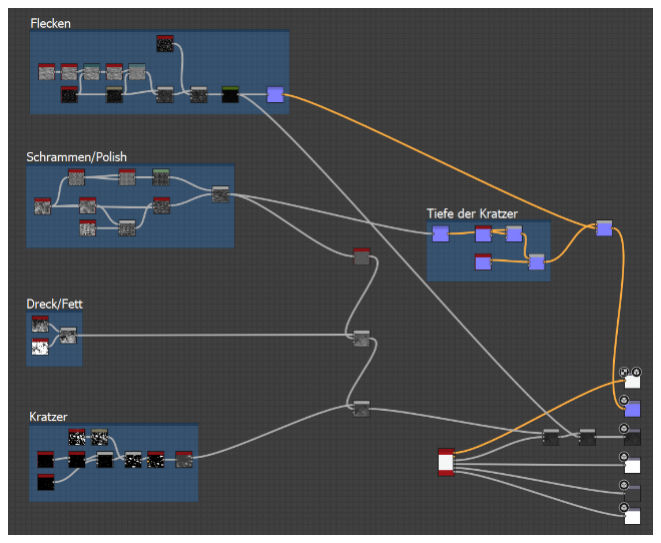
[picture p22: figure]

Das Ziel war es, eine Realistische PBR-Texture in dem dafür bestimmten Programm ,,Substance Designer” zu erstellen und diese dann auf die für die eigens erstellten Modelle zu benutzen. Das Programm ,,Substance Designer” benutzt eine Node-Based Programmierung und war deswegen sehr einfach zu bedienen. Um möglichst realistische Texturen zu erstellen, ist es nötig mehrere unterschiedliche Texture-Maps zu erstellen, die verschiedenen Informationen für die physikalisch korrekte Darstellung in dem Vorgesehenen Render enthalten. Die Texture sollte
unser verwendetes Aluminiumblech nachah-

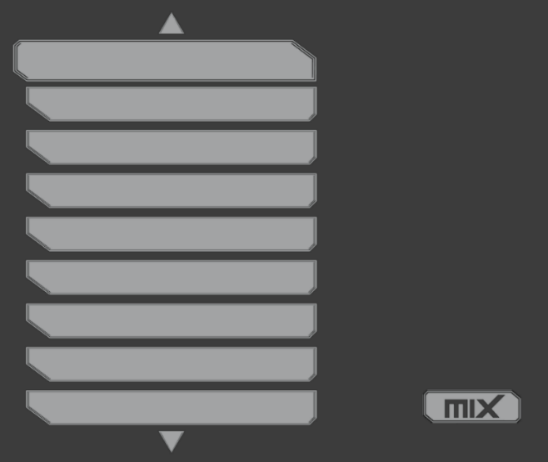
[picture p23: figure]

men. Im Folgendem werde ich die Node-Based-Programmierung für die Erstellung der Texturen erklären. Für die Erstellung der Textur bearbeitete ich hauptsächlich die Roughness-Map ,die die Rauheit der Fläche beeinflusst und die Normal-Map, die die Position der verschiedenen Normalvektoren der einzelnen Flächen um einen festgelegten Wert verschiebt. Um diese ,,Maps” zu kreieren benutzt man 16 Bit Greyscale Images. Diese werden dann mit verschiedenen Operatoren und Algorithmen modifiziert, bis das gewünschte Ergebnis erreicht wird. Um das Erklären der Programmierung zu vereinfachen, werden die einzelnen Effekte aufgeteilt.

Abbildung 57: fertige Ansicht Recipes

Abbildung 58: PBR Überblick

Zu Beginn wurde eine Voreinstellung, die das Erstellen solcher PBR-Texturen vereinfacht, benutzt. Diese Voreinstellung kreierte die nötigen Outputs, um in diesem Fall ein Aluminium-Blech darzustellen. Das Programm übernahm dafür die korrekte Erstellung der Albedo-Map, was die Farbe des Metalls bestimmt, der Metallic-Map, die die metallischen Eigenschaften der Texturen beeinflusst, die Heigth-Map, die,
wenn nötig, die Tiefe oder Höhe der enthaltenden Informationen beeinflusst und die Ambient
Oclusion-Map , die, wenn nötig, Lichtinformationen zur korrekten Beleuchtung in einer vorher bestimmten Umgebung speichert.

Es wurden eine Reihe von verschiedenen Effekten erstellt. Darunter befinden sich Flecken, Schrammen, Fettschichten und Kratzer für die fehlenden beiden Texture-Maps.

Um die Kratzer zu erstellen, benutzte ich einen Algorithmus, der ein Greyscale-Image erstellt, wo Kratzer generiert werden.
Von dieser erstellte ich zwei unterschiedliche Versionen, wovon
ich die eine mit der Funktion ,,Slope Blur” modifiziert habe damit diese nicht mehr so stark vorkommt. Diese beiden Bilder wurden dann mit der Funktion ,,Blend” stark verschwommen
und wurden dann mit der Funktion ,,Blend” zusammengefügt.

Daraufhin benutzte ich eine Grungemap, die zuvor mit der Funktion ,,Blur” bearbeitet wurde, und fügte diese mit den zusammengefügten Kratzerbildern zusammen. Diese neu erstellte Map wurde dann mit der Funktion ,,Vector Morph” manipuliert, in
dem man das sekundäre Vektorfeld der Textur verändert. Die Texturen
wurden dann mit der Funktion ,,Heigth Map Frequencies” bearbeitet,
was zur Folge hat, dass das Bild in zwei verschiedene Texture-Maps transferiert wird. Diese wurden später weiter genutzt.

Die Fettflecken wurden mit zwei unterschiedlichen Grunge-Maps erstellt, die ich anschließend miteinander multipliziert habe, um den Effekt dieser zu verstärken.

Abbildung 60: Voreinstellungen

Abbildung 59: Kratzer

Abbildung 61: Fettflecken

Um die Schrammen zu erstellen, benutzte ich eine BnW Spots Texture-Map, die ich anschließend mit der Funktion ,,Safe Transform”, ,,Blur HQ” und ,,Slope Blur bearbeitete. Dies hatte zur Folge, dass ich jetzt zwei Versionen dieses Greyscale Images hatte. Eine Version, die verschwommen war, und die andere
wurde auf der X und Y vervielfältigt, sodass ein Raster entsteht. Das
Verschwommene wurde anschließend mit einem Anistropic Noise multipliziert, um den Effekt zu verstärken. Diese wurde dann anschließend durch die Funktion ,,Slope
Blur” verschwommen. Im Anschluss daran wurde dieses Bild mit

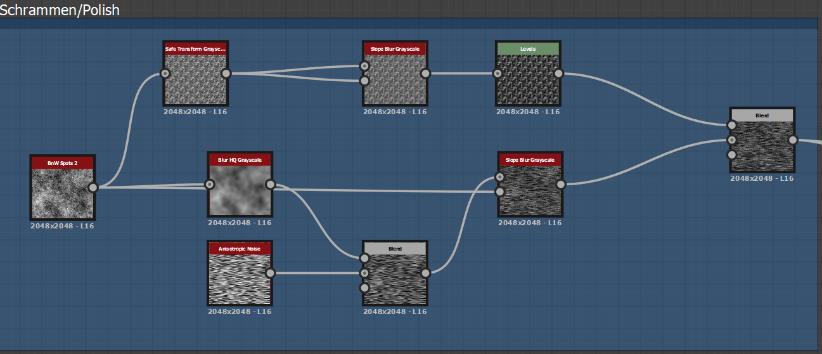
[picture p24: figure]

dem vervielfältigten Musterbild zusammengefügt um dies später weiter zu benutzten.

Die Flecken wurden mittels einem Directional Noise Greyscale Image erstellt, was später mit einem Dirt und Gaussian Spots Image zusammengefügt wurde. Das Directional Noise Image wurde durch die Funktionen ,,Invert”, ,,Directional Warp”, ,,Skew” und ,,Warp” modifiziert. Die Funktion Invert hatte den Effekt die Graustufen zu invertieren. Dieses Bild wurde dann von der Funktion ,,Directionl Warp” in eine bestimmte Richtung verzehrt. Die Funktion ,,Warp” hat den gleichen Effekt nur das dieser auf eine andere Art und Weise das Bild verzehrt. Die Stärke dieses Effektes wurde von dem Greyscale Image ,,Dirt” kontrolliert. ,,Skew” hingegen transformiert das Bild mit verschiedenen Parametern. Nach dem Zusammenfügen der besagten Bilder wurden diese noch ein letztes Mal mit der Funktion ,,Curves” bearbeitet, die die Stärke der Graustufen verändert. Für weiterführenden Arbeiten wurde aus diesem Output mit der Funktion ,,Normal” eine Normal-Map erstellt, die später weiterverarbeitet wurde.

Für den Effekt tieferer Kratzer wurde der Output der Schrammen in eine Normal-Map konvertiert und mit zwei ,,Scratch Generator”-Funktionen zusammengefügt.

Für die letztendliche Normal-Map wurden der Output der tieferen Kratzer und der Output der Flecken zusammengefügt und in den Material Input eingeführt.

Die Roughness-Map wurde durch die Zusammenführung der Outputs der Schrammen, Fettflecken, Kratzer, Flecken und dem voreingestellten Aluminiums Output hergestellt.

Abbildung 62: Schrammen

Abbildung 63: tiefe Kratzer

Rendering der Benutzeroberfläche

Für das Rendern der Benutzeroberfläche nahm ich die entwickelten Modelle und die PBR-Texturen und importierte beides in das Programm Maya. Jedoch stellte sich bald heraus, dass ein mir bis jetzt noch unbekannter Fehler die Texturen zwar auf programminternen Modellen korrekt darstellt, dies aber nicht tut, wenn es ein importiertes Modell meinerseits war. Dieses Problem umging ich, indem ich zu dem Programm Blender wechselte, und dort die Benutzeroberfläche renderte. Die Texturen wurden in die für sie vorgesehenen Inputs des programmierten Shaders angeschlossen, hatten aber nicht den vorgesehenen Effekt. Die Bildauflösung wurde auf 800*600 Pixel gestellt. Die Flächen wurden alle einzeln gerendert, da dies nötig war, damit das Programm von Arvid mit den Bildern keine Leistungsprobleme erzeugt.

Für die Belichtung der Szene nutzte ich eine HDRI von der Seite HDRI Haven.com. Dort werden verschiedenen HDRIs für nicht kommerziellen Nutzen kostenlos zur Verfügung gestellt. Meine Wahl fiel auf die HDRI,, Satara Night (no Lamps)” da diese das Bild nicht überbelichtete.

Hintergrund

Den Hintergrund erstellte ich in dem Programm Blender, indem ich einen Shader programmierte. Dazu benutzte ich den integrierten Principal BDSF Shader und ließ bestimmte Parameter von Noise steuern. In diesem Fall ließ ich den Wert des Roughness Parameters durch eine Noise-Textur, die von einer Color Ramp abgeschwächt wird und einem Wert bestimmen. Des Weiteren wurde eine Noise Textur und eine Bump-Map zum Steuern des Normal-Map Parameters genutzt. Es entstanden zwei Versionen des Hintergrundes. Die eine verwendete die PBR-Aluminium-Textur und die andere den entwickelten Shader. Das gewählte Model für das Rendern war ein Quadrat.

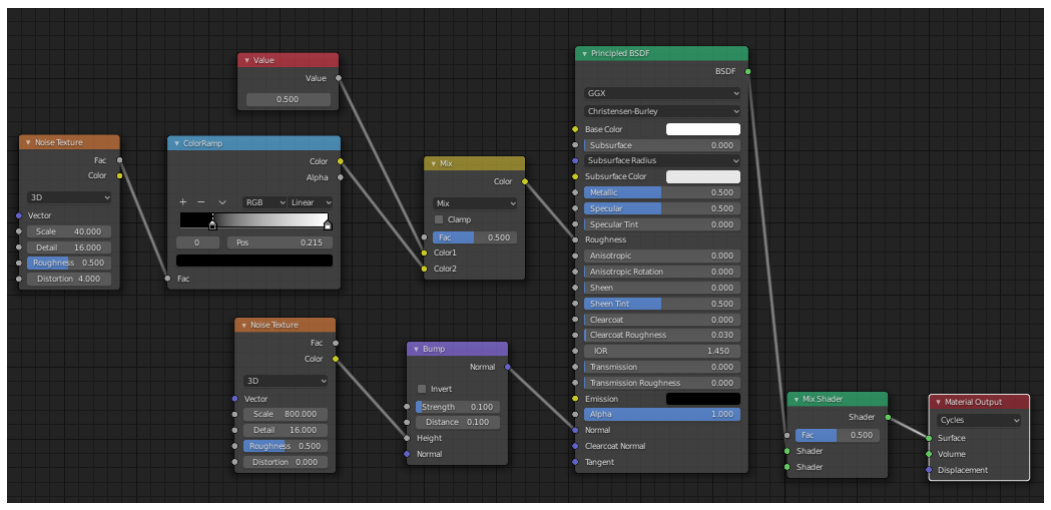
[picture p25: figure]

Abbildung 65: Shader Hintergrund

5.11.10. POSTPROCESSING

Benutzeroberfläche

Auf Anfrage unseres Programmierers Arvid mussten die gerenderten Bilder der Benutzeroberfläche und die einzelnen Komponenten auf ihre individuelle Bildgröße zugeschnitten werden. Die Bildgröße wurde mittels Quadrate um die verschiedenen Modelle ermittelt. Dies war nötig, um diese Bilder in dem Programm als eigentliche Benutzeroberfläche zu benutzen und in Echtzeit die verschiedenen Bilder auf die richtigen Positionen zu verschieben. Das Zuschneiden der zugehörigen Flächen erfolgte, in dem Bildbearbeitungsprogramm Pixlr, womit die verschiedenen Bilder importiert und zugeschnitten worden sind.

Die Versionen, die indizieren, dass eine Fläche ausgewählt worden ist, wurde aus den zugeschnittenen Versionen hergestellt. Dazu programmierte ich in dem Programm Blender mit Node-Based-Programming einen Algorithmus, der die Bilder farblich so modifiziert wie dies auch programmiert wurde. Als dieser Algorithmus fertig war, musste man nur noch die gewünschten Bilder als Input angeben und das Bild neu rendern. Dies wurde mit allen erwünschten Versionen gemacht.

Die Programmierung lief wie
folgt ab: Das
Bild erfährt
durch die Funktion ,,Color Balance” verschiedene Farbveränderungen, die
festlegen, wie jeder Pixel dargestellt wird. Dieser Output wird dann danach von der Funktion ,,RGB Curves” weiterverarbeitet. Diese Funktion verändert auch wieder die Farbverhältnisse der verschiedenen Farbkanäle um den Wert der eingestellten Kurve. Um den entstandenen Noise komplett zu entfernen, wird das Bild noch durch einen Denoiser geschickt, der diese Fehler behebt, indem er die fehlenden Pixel füllt.

Abbildung 68: Algorithmus zum Ändern der Benutzeroberfläche


Abbildung 67: Vor dem
Postprocessing

Abbildung 66: Nach dem
Postprocessing

Hintergrund

Das erste fertig-gerenderte Bild für den Hintergrund verlor durch Überbelichtung sein Detail-Reichtum und wurde überwiegend Weiß. Durch das Postprocessing konnte ich diesen Fehler beheben. Dafür benutzte ich wieder die Funktion ,,Color Balance” um der Helligkeit entgegenzuwirken und das Bild einen Grau-Ton zu verpassen. Die danach verwendete Funktion ,,Color Ramp” dient dazu, die verschwundenen Details wieder zum Vorschein zu bringen. Zur Verfeinerung der Konturen und Kontraste verwendete ich danach die beiden Funktionen ,,Bright/Contrast” und ,,Hue Saturation Value”. Danach benutzte ich noch einen Denoiser, um das Bild von entstandenen Fehlern zu beheben.


Abbildung 69: Algorithmus für den Hintergrund


Abbildung 71: Hintergrund vor dem Postprocessing | Abbildung 70: Hintergrund nach dem Postprocessing

5.11.11. SCHLUSSWORT ZUR BENUTZEROBERFLÄCHE

Während der kompletten Entwicklung stand ich mehrmals am Abgrund der Verzweiflung. Durch die eigenen Fehlentscheidungen und Taten wurden mehrerer Stunden verschwendet. Diese Entscheidungen waren aber nötig, damit das Projekt bis zur jetzigen finalen Version gelangen konnte. Persönlich habe ich einige neue und nützliche Lehren aus diesem Projekt gezogen. Des Weiteren hoffe ich, dass diese Dokumentation Ihnen einen Einblick in dieses Themengebiet gegeben hat und Sie es auch verstanden haben. Es steht nicht außer Frage, dass meine Vorgehensweise dieser Benutzeroberfläche nicht die effektivste war und es bessere standardisierte Vorgehensweisen existieren. Trotz dessen bereue ich es nicht, so viel Zeit in dieses Projekt gesteckt zu haben. Wohlmöglich hätte ich eines Tages genau den gleichen Stand wie jetzt erreicht, aber durch den Druck, den das Projekt auf die einzelnen Projekt-Mitglieder ausgeübt hat, wurde ein schnelles Anpassen an die gegebenen Umgebungen erzwungen. Persönlich gesehen war es in vollen Zügen ein erfolgreiches Projekt, selbst wenn die Benutzeroberfläche doch noch besser sein könnte.

5.12. INBETRIEBNAHME UND TESTEN DES GERÄTES
5.12.3. TESTEN DER MASCHINE

Nach mehreren Testläufen mit verschiedenen Einstellungen hat sich ergeben, dass die Maschine ihre Funktion zwar erfüllt, aber die Geschwindigkeit der Flüssigkeitsbeförderung zu wünschen übriglässt. Außerdem erwiesen sich die Schnellspannsysteme als nicht geeignet für Flüssigkeiten, da einige Lecks erschienen.

5.12.4. TESTEN DER BENUTZEROBERFLÄCHE

Um das Programm, bzw. die Benutzeroberfläche fertigzustellen, haben wir, also Dominic und Arvid, uns einen Tag lang zusammengesetzt und Stück für Stück die Bilddateien, aus denen die Oberfläche besteht, eingebaut und getestet. Dabei haben wir noch kleine Details angepasst, zum Beispiel das Verhalten der Pfeile am oberen und unteren Ende der Listen.

6. FAZIT

Das gesamte Projekt hat sich als spannende und interessante Erfahrung herausgestellt. Es war eine angenehme Alternative zum Frontalunterricht mit theoretischen Inhalten. Wir hatten das Gefühl, dass wir mal was Nützliches fürs Leben lernten und es auch in Zukunft gebrauchen könnten.

Unser größtes Problem während des ganzen Zeitraums des Projektes war die Pandemie. Da es vorgesehen war, sich außerhalb der Schule zu treffen, um daran gemeinschaftlich zu arbeiten, wäre man nicht gezwungen alles in der Schule zu erledigen. Uns war es jedoch verboten sich in größeren Gruppen zu treffen. Also fielen diese Gelegenheiten aus. Am Ende blieben uns nur die 90 Minuten in den regulären Einheiten des Praxisunterrichts, sowie gelegentliche Ausfälle anderer Lehrkräfte um uns aktiv als Gruppe um das Projekt zu kümmern. Deswegen haben wir auch eine komplette Woche der Osterferien geopfert, wo wir jeden Tag 6 bis 8 Stunden am Projekt arbeiten konnten. Genau in der Zeit hatten wir auch das Gefühl, dass wir große Fortschritte gemacht haben.

Wir haben zum größten Teil unsere gestellten Ziele erreicht. Sie entnimmt mit der Pumpe die Flüssigkeiten und befördert sie in ein Glas. Zumindest zum Großteil. Uns ist recht spät aufgefallen, dass die Größe der Pumpe zu klein ausgefallen ist. Das bedeutet, sie transportiert sehr wenig Flüssigkeiten. Außerdem sind die Schnellanschlüsse undicht und ziehen dauerhaft Luft in das System, was dazu führt, dass die Menge der transportierten Flüssigkeiten nochmals verlangsamt wird.

Zu guter Letzt bedanken wir uns bei unseren Lehrkräften für die umfangreiche Unterstützung während des ganzen Projektes. Sie standen uns nahezu jederzeit mit Rat und Tat an der Seite. Auch in den Ferien, und wenn wir sehr kurzfristig ungeplante Zeiten in den Werkstätten verbracht haben.

7. QUELLEN

Fonts:

- Da Mad Rave: https://www.dafont.com/da-mad-rave.font
- Camingo-Code: https://www.fontsquirrel.com/fonts/camingocode

HDRIs:

- Goegap: https://hdrihaven.com/hdri/?h=goegap
- Satar Nigh (no lamps): https://hdrihaven.com/hdri/?h=satara_night_no_lamps

Verwendete Python-Module:

- Pygame: https://www.pygame.org/news
- OpenCV: https://opencv.org/
- Numpy: https://numpy.org/
- Tkinter: https://docs.python.org/3/library/tkinter.html
- gpiozero: https://github.com/gpiozero/gpiozero
- zusätzliche Python-interne Module: os, pathlib, time

kopierter Quellcode in der Datei media_lib.py:

- Funktionen für Textumbruch (truncline() und wrapline(), ab ca. Zeile 330): http://www.pygame.org/wiki/TextWrapping?parent=CookBook
- Funktion zur Anzeige des Datei-Dialogs (prompt_file(), ab ca. Zeile 585): https://stackoverflow.com/questions/63801960/how-to-prompt-user-to-open-a-filewith-python3-pygame (https://stackoverflow.com/questions/63801960/how-to-prompt-user-to-open-a-file-with-python3-pygame)

Alle Webseiten zuletzt besucht am: 10.5.21, 15:00

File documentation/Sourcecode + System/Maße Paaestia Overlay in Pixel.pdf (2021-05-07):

Maße:
Haupt Menü:


Nummer | Höhe in px | Breite in px | Position (X/Y)
A1 | 439 | 197 | (48 / 552)
A2 | 484 | 279 | (261/ 587 )
A3 | 439 | 197 | ( 557 / 552 )
A4 | 77 | 250 | ( 274 / 89 )

Maße Setting Tabs:


Nummer | Höhe in px | Breite in px | Position (X/Y)
B1 | 582 | 326 | ( 14 / 590 )
B2 | 582 | 326 | ( 461 / 590 )


Maße Rezepte:

Nummer | Höhe in px | Breite in px | Position (X/Y)
C1 | 30 | 35 | ( 283/ 37 )
C2 | 30 | 35 | (283/ 593 )
C3 | 56 | 404 | ( 90 / 556 )
C4 | 47 | 388 | (107 / 494 )
C5 | 45 | 131 | ( 635 / 91 )

Die Position von Fläche 4 zur nächsten Fläche 4 verschiebt sich um 58 pixel auf der Y-Achse nach unten

Der Abstand zwischen 4 und 4.1 beträgt 12 Pixel

Der Abstand zwischen 3 und 4 beträgt 7 Pixel


Der Abstand zwischen 3 und 3.1 beträgt 5 Pixel

Die Position von Fläche drei verschiebt sich um 60 Pixel auf der Y- Achse nach unten

Maße Select Drinks Liste:

Abstände sind genau wie bei Maße Rezepte


Nummer | Höhe in px | Breite in px | Position (X/Y)
D1 | 30 | 35 | (383 / 37 )
D2 | 30 | 35 | (383/ 594 )
D3 | 56 | 366 | (188 / 557 )
D4 | 56 | 92 | (537 / 557 )
D5 | 47 | 388 | (206 / 494 )

Maße Import Cocktails:

Abstand genau gleich wie bei Maße Rezepte:


Nummer | Höhe in px | Breite in px | Position (X/Y)
E1 | 30 | 35 | ( 283/ 37)
E2 | 30 | 35 | ( 283/ 594 )
E3 | 56 | 409 | ( 87 / 557 )
E4 | 47 | 393 | ( 104/ 494 )
E5 | 45 | 131 | ( 635 / 90 )

Maße Frei Mischen:


Nummer | Höhe in px | Breite in px | Position (X/Y)
Turm 1 10% | 30 | 45 | ( 104 / 208 )
Turm 1 20% | 54 | 40 | ( 127 / 232 )
Turm 1 30 % | 61 | 31 | ( 127 / 255 )
Turm 1 40% | 63 | 31 | (127 / 280 )
Turm 1 50% | 63 | 31 | ( 127 / 306)
Turm 1 60% | 63 | 31 | (127 / 331 )
Turm 1 70% | 63 | 31 | ( 127 / 356 )
Turm 1 80% | 63 | 31 | (127 / 381 )
Turm 1 90% | 63 | 31 | ( 127 / 405 )
Turm 1 100% | 75 | 45 | ( 113 / 443 )
Turm 2 10% | 30 | 45 | ( 186 / 208 )
Turm 2 20% | 54 | 40 | ( 167 / 232 )
Turm 2 30 % | 61 | 31 | ( 176 / 255 )
Turm 2 40% | 63 | 31 | ( 176 / 280 )

Turm 2 50% | 63 | 31 | ( 176 / 306 )
Turm 2 60% | 63 | 31 | ( 176 / 331 )
Turm 2 70% | 63 | 31 | ( 176 / 356 )
Turm 2 80% | 63 | 31 | ( 176 / 381 )
Turm 2 90% | 63 | 31 | ( 176 / 405 )
Turm 2 100% | 75 | 45 | ( 176 / 443 )
Turm 3 10% | 30 | 128 | ( 337 / 208 )
Turm 3 20% | 54 | 80 | ( 361 / 232 )
Turm 3 30% | 61 | 80 | ( 361/ 255 )
Turm 3 40% | 63 | 80 | ( 361 / 280 )
Turm 3 50% | 63 | 80 | ( 361 / 306 )
Turm 3 60% | 63 | 80 | ( 361 / 331 )
Turm 3 70% | 63 | 80 | ( 361 / 356 )
Turm 3 80% | 63 | 80 | (361 /381 )
Turm 3 90% | 62 | 80 | ( 361 / 405 )
Turm 3 100% | 75 | 108 | ( 347 / 443 )
Turm 4 10% | 30 | 45 | ( 570/ 208 )
Turm 4 20% | 54 | 40 | ( 594 / 232 )
Turm 4 30% | 61 | 31 | ( 594 / 255 )
Turm 4 40% | 63 | 31 | ( 594 / 280 )
Turm 4 50% | 63 | 31 | ( 594 / 306 )
Turm 4 60% | 63 | 31 | (594 / 331 )
Turm 4 70% | 63 | 31 | ( 594 / 356 )
Turm 4 80% | 63 | 31 | ( 594 / 381 )
Turm 4 90% | 62 | 31 | ( 594 / 405 )
Turm 4 100% | 75 | 45 | (580 / 443 )
Turm 5 10% | 30 | 45 | ( 652 / 208 )
Turm 5 20% | 54 | 40 | (634 / 232 )
Turm 5 30% | 61 | 31 | ( 643 / 255 )
Turm 5 40% | 63 | 31 | ( 643 / 280 )
Turm 5 50% | 63 | 31 | ( 643 / 306 )
Turm 5 60% | 63 | 31 | ( 643 / 331)
Turm 5 70% | 63 | 31 | (643 / 356 )
Turm 5 80% | 63 | 31 | ( 643 / 381 )
Turm 5 90% | 62 | 31 | ( 643 / 405 )
Turm 5 100% | 377 75 | 221 45 | (643 / 443) 6 ( 57 / 485 )

7 | 377 | 221 | ( 290 / 485 ) 8 | 377 | 221 | ( 523 / 485 ) 9 | 39 | 112 | ( 345 / 565)
10 | 69 | 495 | ( 153 / 583 )
11 | 52 | 64 | ( 47 / 85 )
12 | 52 | 64 | ( 704 / 85 )

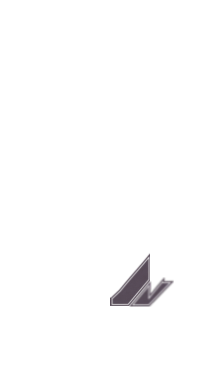
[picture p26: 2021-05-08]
code/src/media/free/tower_5/c.png

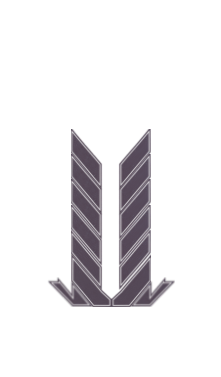
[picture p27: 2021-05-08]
code/src/media/free/tower_3/h.png

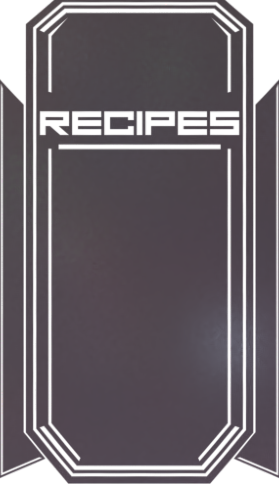
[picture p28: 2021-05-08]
code/src/media/main_menu/recipes.png

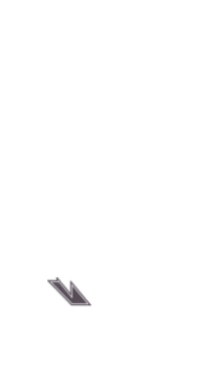
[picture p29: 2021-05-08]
code/src/media/free/tower_4/b.png

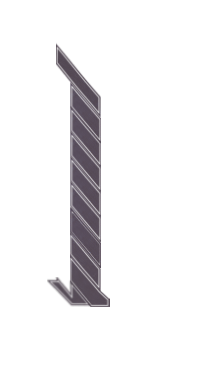
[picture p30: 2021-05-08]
code/src/media/free/tower_1/k.png

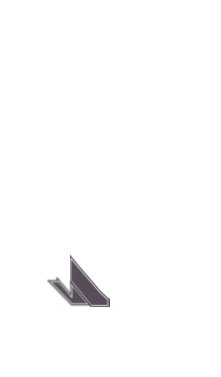
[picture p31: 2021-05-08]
code/src/media/free/tower_1/c.png

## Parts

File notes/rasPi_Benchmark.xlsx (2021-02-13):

Auflösung | Sprites, 24 FPS | Sprites, 150 FPS | Video mit opencv, 24 FPS | Sprites | Video mit opencv | FPS
 |  |  |  | Wiedergabe mit eizelnen Bilddateien (png), die nacheinander abgespielt werden | Wiedergabe einer Videodatei (mp4) mit dem opencv-Modul | Die Begrenzung der Framerate im Skript. Das Program wartet jede Runde, bis die Framerate eingehalten wird.
1280 x 1024 | 12
1440 x 900 | 12
1280 x 960 | 12
1152 x 864 | 14
1280 x 720 | 16 |  | 14
1024 x 768 | 19 | 19 | 15.7
800 x 600 | 23 | 30 | 24
720 x 480 | 24 | 40 | 24
640 x 480 | 24 | 46
720 x 400 | 24 | 49
24
24
24
24
24
24
24
24
24
24

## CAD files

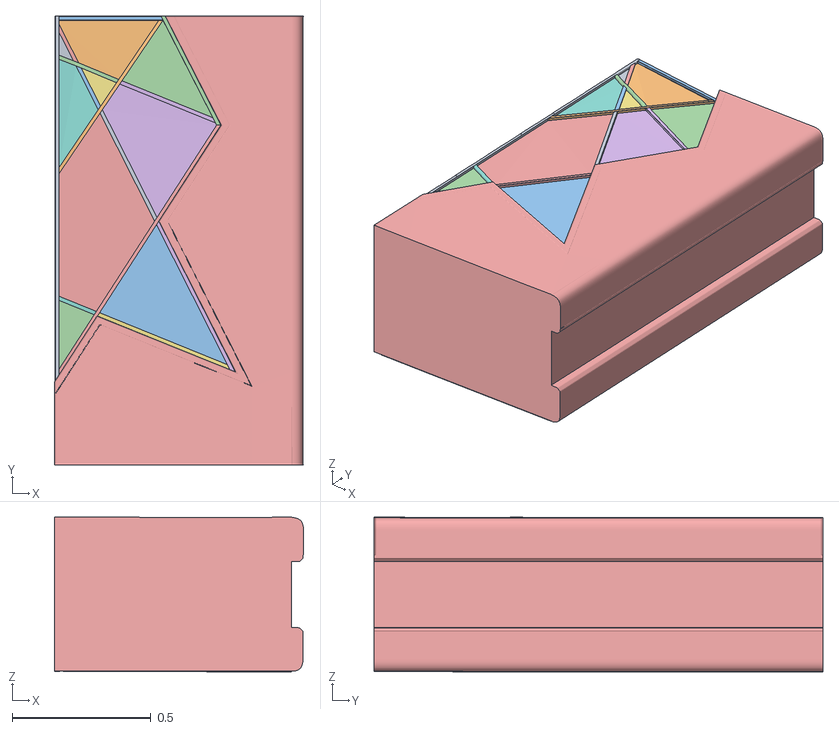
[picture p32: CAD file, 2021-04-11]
documentation/Pläne + Skizzen/3D-Modelle/Finished Automat.OBJ
0.899 x 1.62 x 0.559
Finished_Automat
Finished_Automat.001
Finished_Automat.002
Finished_Automat.003
Finished_Automat.004
Finished_Automat.005
Finished_Automat.006
Finished_Automat.007
Finished_Automat.008
Finished_Automat.009
Finished_Automat.010
Finished_Automat.011
Finished_Automat.012
Finished_Automat.013
Finished_Automat.014
Finished_Automat.015
Finished_Automat.016
Finished_Automat.027
Finished_Automat.028
Finished_Automat.029
Finished_Automat.030
Finished_Automat.031
Finished_Automat.032
Finished_Automat.033
Finished_Automat.034
Finished_Automat.035
Finished_Automat.036
Finished_Automat.037
Finished_Automat.038

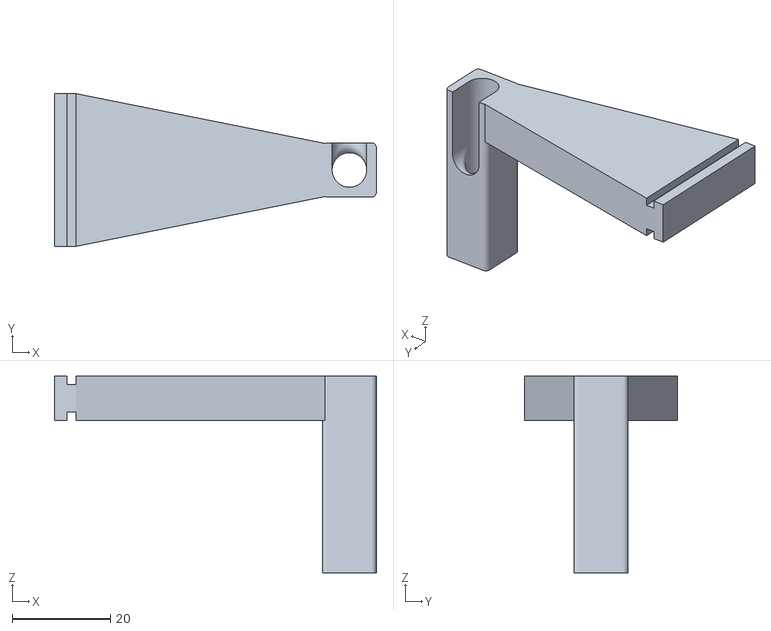
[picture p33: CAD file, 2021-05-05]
documentation/Technische Zeichnungen + CAD-Modelle/Fusion 360 - CAD-Dateien/Auslass Mount/v3/Mount.stl
65.4 x 31.0 x 40.0

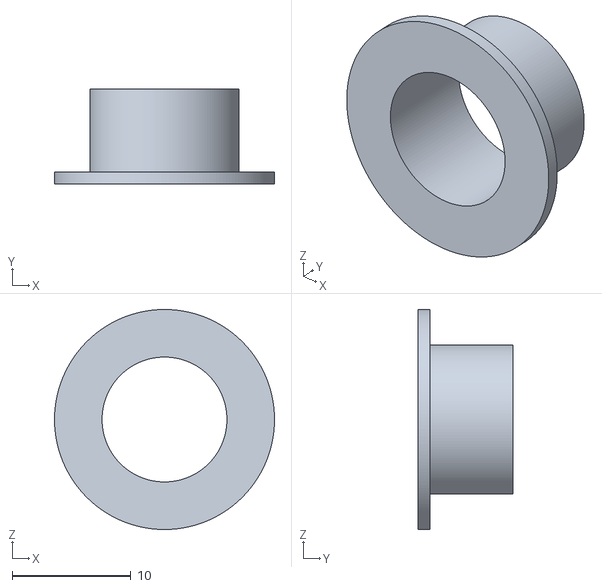
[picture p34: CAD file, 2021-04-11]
documentation/Technische Zeichnungen + CAD-Modelle/Fusion 360 - CAD-Dateien/DC-Stecker Mount/v1/Mount.stl
18.5 x 8.00 x 18.5

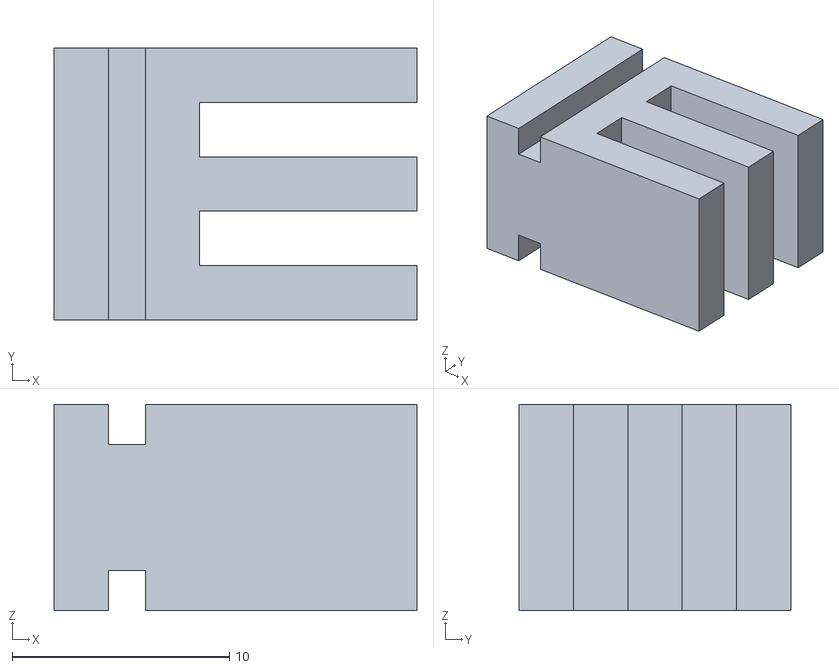
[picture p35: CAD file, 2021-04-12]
documentation/Technische Zeichnungen + CAD-Modelle/Fusion 360 - CAD-Dateien/Flaschen Mount/v2/Klammern oben/Schlitten.stl
16.7 x 12.5 x 9.48

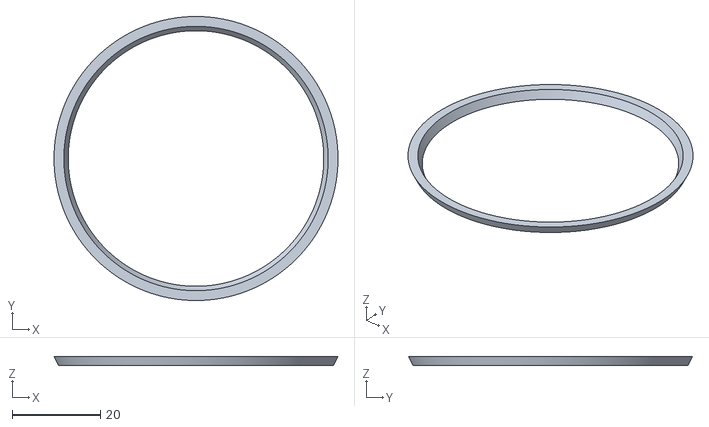
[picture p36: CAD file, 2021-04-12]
documentation/Technische Zeichnungen + CAD-Modelle/Fusion 360 - CAD-Dateien/Flaschen Mount/v2/Trichter unten/Trichter oben.stl
64.5 x 64.5 x 2.00

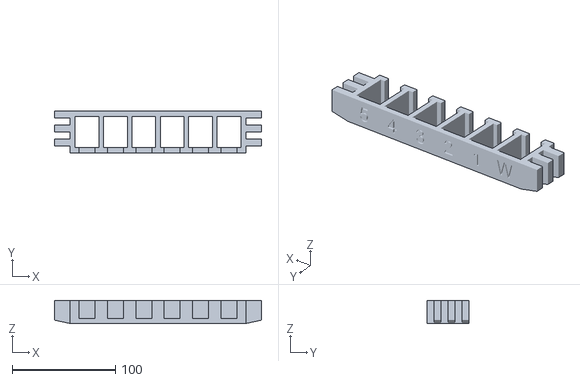
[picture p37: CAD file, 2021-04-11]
documentation/Technische Zeichnungen + CAD-Modelle/Fusion 360 - CAD-Dateien/Magnetventil Mount/v2/Mount mitte.stl
200.5 x 40.5 x 22.5

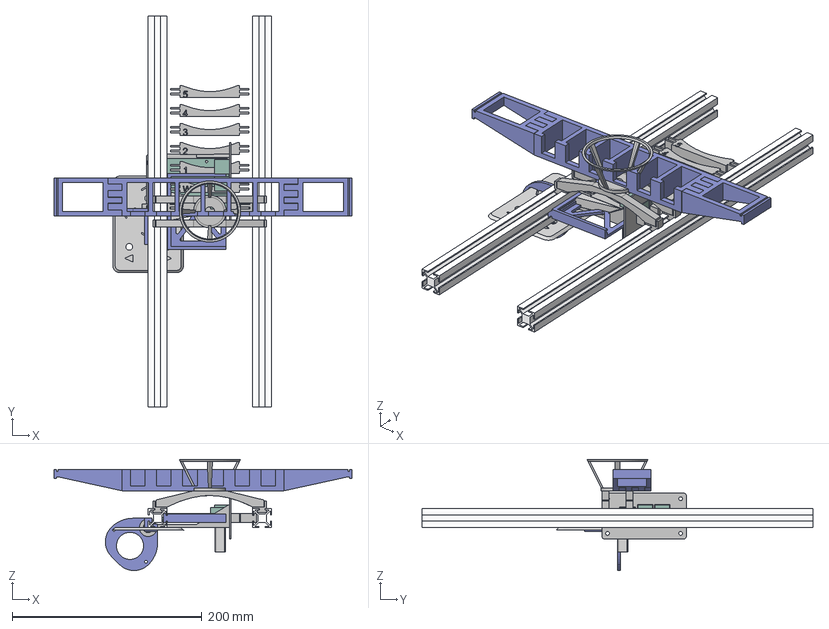
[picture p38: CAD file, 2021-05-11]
documentation/Technische Zeichnungen + CAD-Modelle/Fusion 360 - CAD-Dateien/Paamestia v142.step
313.9 x 411.4 x 116.9 mm
Taster Blende
Pumpe Mount
V2
RasPi Mount
Step-Down-Converter Mount
Relay-Bord Mount
Auslass Mount
DC-Stecker Mount
Mount Oben - Klammern/Schienen
Mount Unten - Trichter

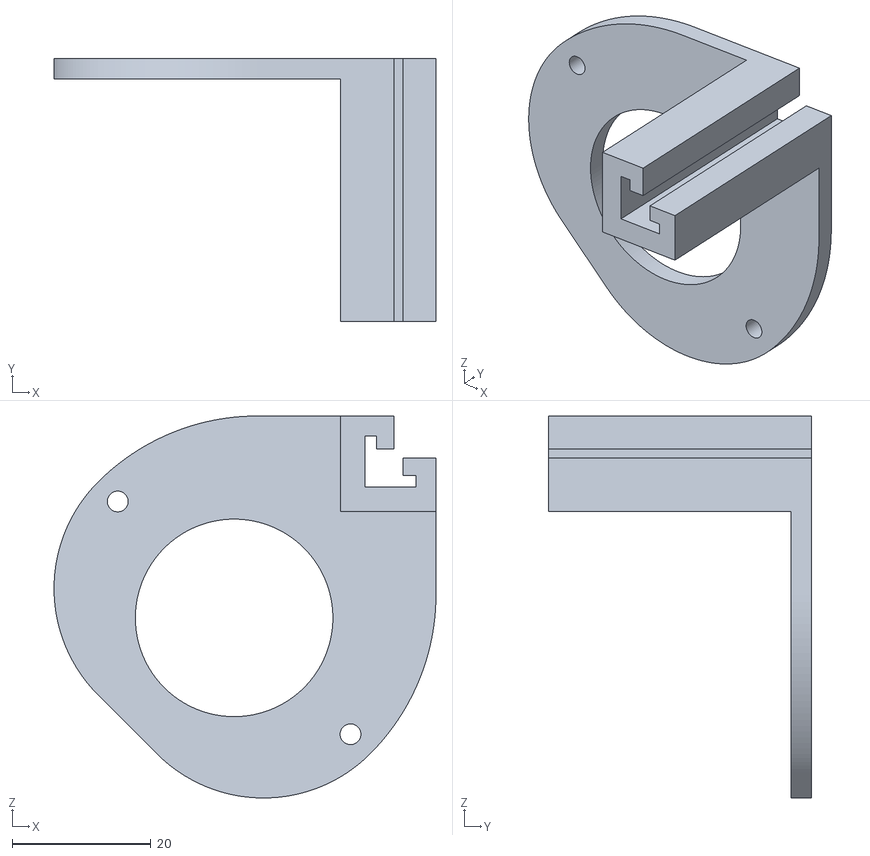
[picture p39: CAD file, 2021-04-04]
documentation/Technische Zeichnungen + CAD-Modelle/Fusion 360 - CAD-Dateien/Pumpe Mount/v3/Mount.stl
55.1 x 38.0 x 55.1

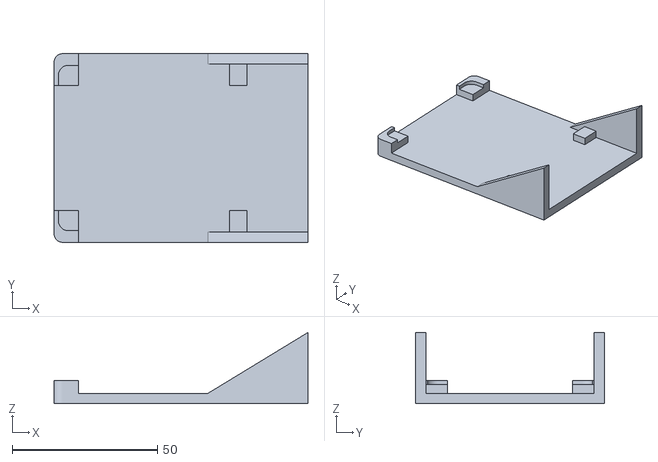
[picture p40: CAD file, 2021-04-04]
documentation/Technische Zeichnungen + CAD-Modelle/Fusion 360 - CAD-Dateien/RasPi-Mount/v2/v2.2/Mount.stl
87.5 x 65.0 x 24.5

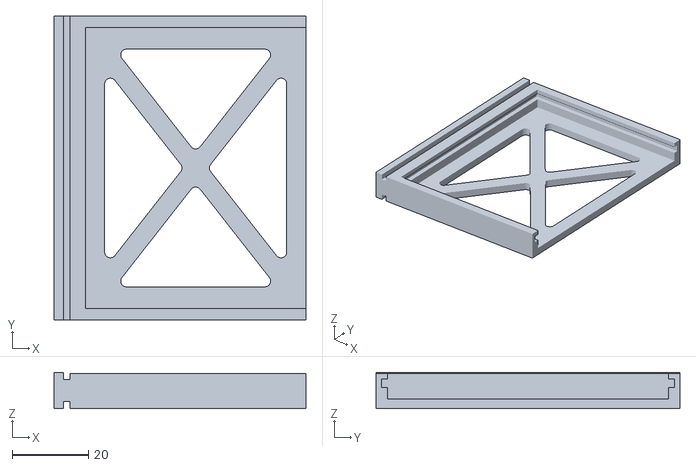
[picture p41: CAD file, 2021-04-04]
documentation/Technische Zeichnungen + CAD-Modelle/Fusion 360 - CAD-Dateien/Relais Board Mount/v2/Mount.stl
65.9 x 79.6 x 9.48

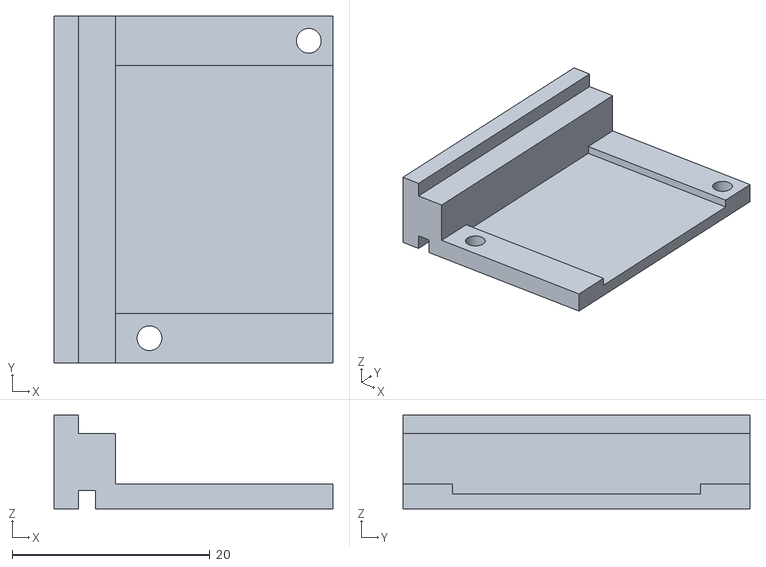
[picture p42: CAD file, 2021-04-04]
documentation/Technische Zeichnungen + CAD-Modelle/Fusion 360 - CAD-Dateien/Step-Down-Converter-Mount/v2/v2.stl
28.2 x 35.1 x 9.48

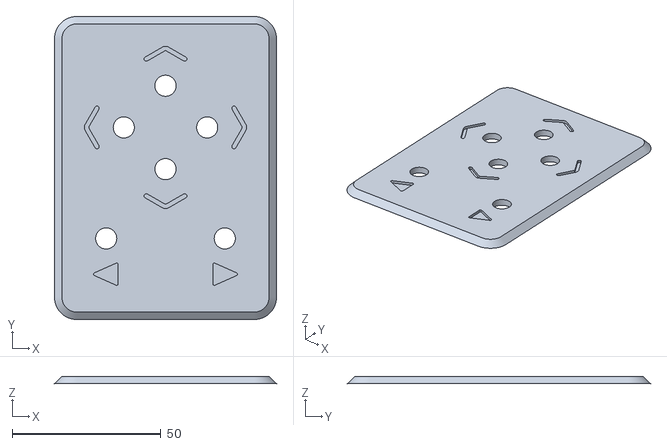
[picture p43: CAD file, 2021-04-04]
documentation/Technische Zeichnungen + CAD-Modelle/Fusion 360 - CAD-Dateien/Taster Blende/v2/Taster Blende.stl
74.5 x 101.8 x 2.50

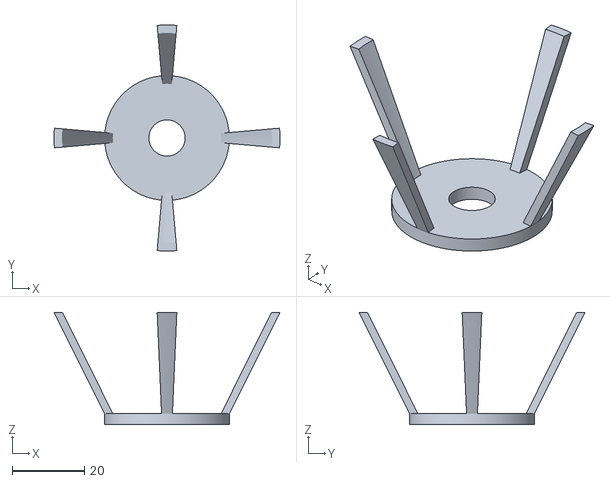
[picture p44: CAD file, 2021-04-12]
documentation/Technische Zeichnungen + CAD-Modelle/Fusion 360 - CAD-Dateien/Flaschen Mount/v2/Trichter unten/Trichter unten.stl
62.5 x 62.5 x 31.0

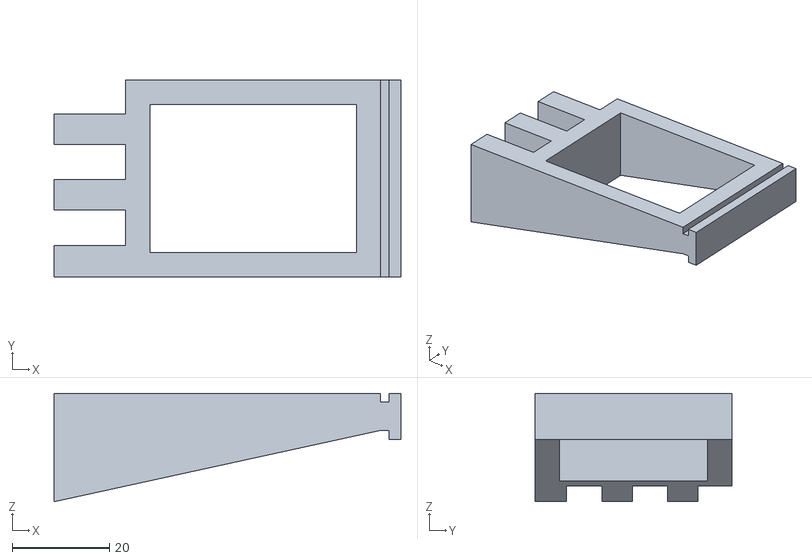
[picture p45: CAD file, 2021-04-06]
documentation/Technische Zeichnungen + CAD-Modelle/Fusion 360 - CAD-Dateien/Magnetventil Mount/v2/Mount rechts 306mm.stl
71.4 x 40.5 x 22.3

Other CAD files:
documentation/Technische Zeichnungen + CAD-Modelle/Fusion 360 - CAD-Dateien/RasPi-Mount/v2/v2.2/Shield.stl
documentation/Technische Zeichnungen + CAD-Modelle/Fusion 360 - CAD-Dateien/Flaschen Mount/v2/Trichter unten/Stütze.stl
documentation/Technische Zeichnungen + CAD-Modelle/Fusion 360 - CAD-Dateien/Magnetventil Mount/v2/Mount links 306mm.stl
documentation/Technische Zeichnungen + CAD-Modelle/Fusion 360 - CAD-Dateien/Flaschen Mount/v2/Trichter unten/Brücke.stl
documentation/Technische Zeichnungen + CAD-Modelle/Fusion 360 - CAD-Dateien/Auslass Mount/v1/Mount.stl
documentation/Technische Zeichnungen + CAD-Modelle/Fusion 360 - CAD-Dateien/Auslass Mount/v2/Mount.stl
documentation/Technische Zeichnungen + CAD-Modelle/Fusion 360 - CAD-Dateien/Flaschen Mount/v1/Körper7.stl
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

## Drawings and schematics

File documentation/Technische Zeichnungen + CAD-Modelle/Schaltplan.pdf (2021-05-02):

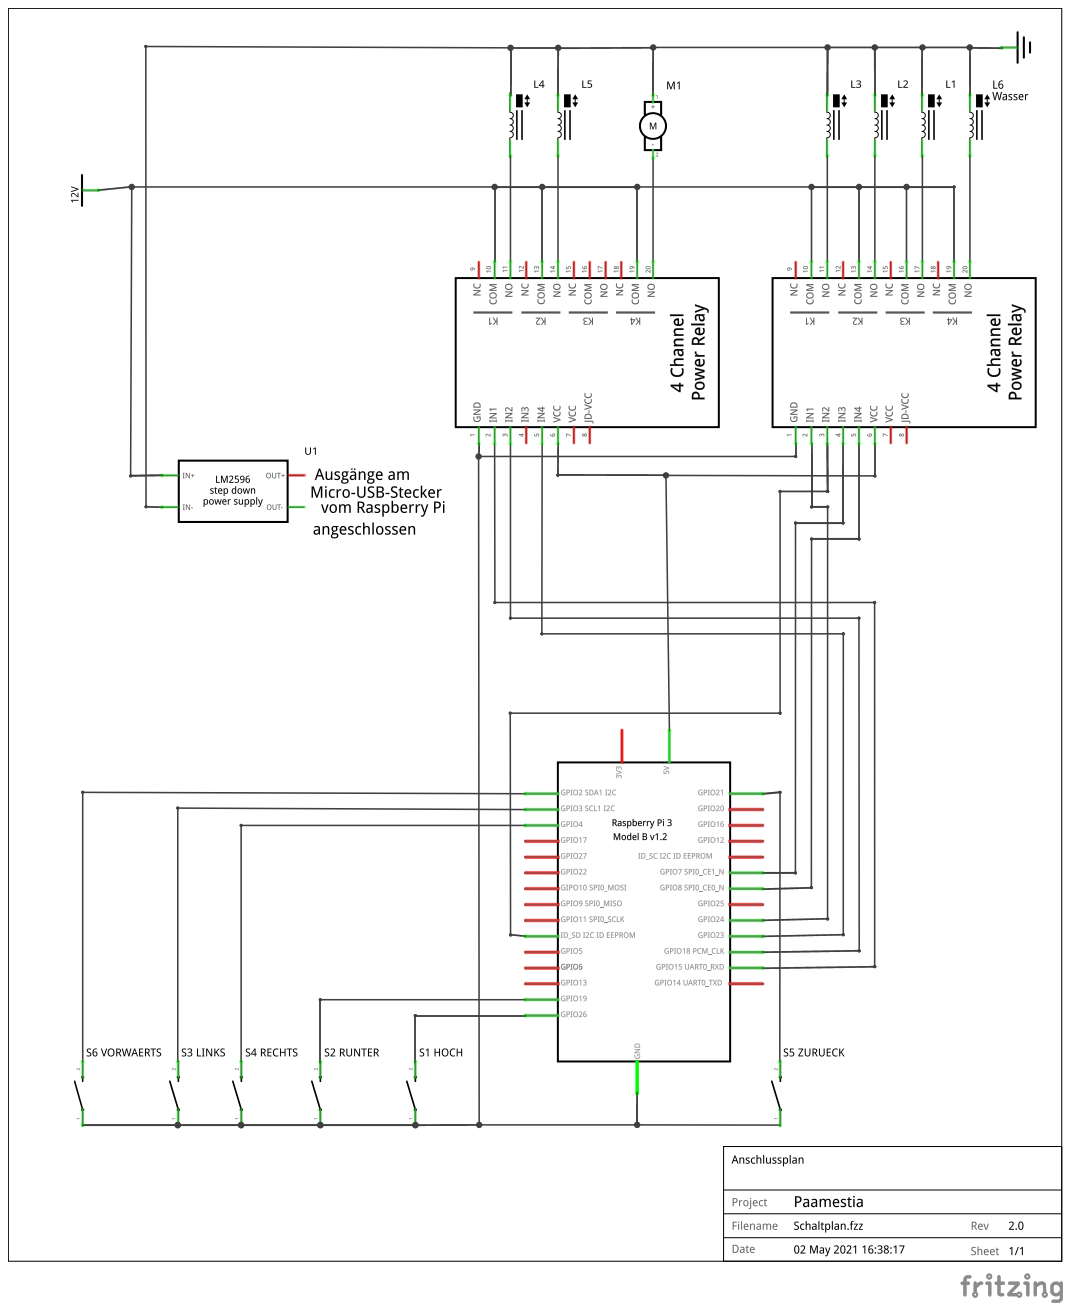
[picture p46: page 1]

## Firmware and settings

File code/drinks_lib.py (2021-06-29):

"""
contains the recipe-class and drink-class
"""

# imports
from tkinter.constants import TRUE
import globals as gl
import io_lib as io
import os
import time
from media_lib import prompt_file		# both used to import new files
from shutil import copyfile

""" ### PATHS ### """
dir_recipes = gl.gen_path + "/src/recipes/"					# path to the recipe-directory

""" ### STORAGE ### """
plugs = ["cleaning_water", "", "", "", "", ""]				# stores the drinks plugged in

drinks = []													# stores the available drinks to choose from

recipes = []												# stores all recipes that could be found in the recipe folder

""" variables for mixing """
is_mixing = False				# stores if currently a recipe is mixing
recipe_step = 0					# stores the current step
commands = []					# compiled command lines
finishing_time = 0				# precalculated time for when the timer will be done

""" functions """
def current_milli_time():
	# returns the current unix-time in milliseconds
    return round(time.time() * 1000)


""" ### SETUP ### """
# this part will run once, as soon this file is imported somewhere

def update_recipes_and_drinks():
	""" updates the recipe and drinks list"""
	global drinks, recipes
	drinks.clear()
	recipes.clear()

	# look for drinks
	file1 = open(gl.gen_path + "/src/drinks", 'r')			# open file
	drinks = file1.readlines()								# save lines as a list
	file1.close()
	file1 = open(gl.gen_path + "/src/drinks_custom", 'r')			# open file
	drinks += file1.readlines()								# save lines as a list
	file1.close()

	for idx, i in enumerate(drinks):						# remove trailing newline characters
			if drinks[idx].endswith('\n'):
				drinks[idx] = drinks[idx][:-1]
				
	print("[DR URD] drink list  content:")
	print(drinks)

	# look for recipes
	for filename in os.listdir(dir_recipes):
		recipes.append(filename)
	recipes.remove('free_mixed_recipe')				# sort out the free mixed recipe, as it should not appear in the recipe list

	print("[DR URD] recipe list  content:")
	print(recipes)

	# sort lists
	if gl.os_is_linux:
		drinks.sort()
		recipes.sort()

update_recipes_and_drinks()

""" ### TEST AVAILABILITY ### """
def _test_availability(recipe):
	""" tests if the needed drink for a recipe are plugged in. returns bool
	recipe: recipe name [str]
	"""
	global drinks

	file1 = open(dir_recipes + recipe, 'r')					# open file
	needed_drinks = file1.readlines()							# save lines as a list
	file1.close()

	needed_drinks.pop(0)			# remove info line

	for idx, i in enumerate(needed_drinks):						# loop thorugh every drink in list
		if needed_drinks[idx].endswith('\n'):						# remove trailing newline characters
			needed_drinks[idx] = needed_drinks[idx][:-1]

		c_idx = needed_drinks[idx].find(',')						# remove volume information
		needed_drinks[idx] = needed_drinks[idx][:c_idx]
	
	for d in needed_drinks:
		if not d in plugs:
			#print("DR TA d: " + str(d))
			return False												# return False, if drink d is not plugged in
	
	return True															# return True, as everything seems to be there


""" ### set drinks ### """
def set_drink(plug, drink):
	""" set drink
	plug: number of the plug (1-6) [int]
	drink: EITHER drink name or "None" for reset [string] OR index for drinks list (1-end of list, because 0 is cleaning_water) (-1: reset) [int]
	"""
	global drinks, plugs

	if plug < 1 or plug > len(plugs)-1:
		return					# break when wrong plug given
		
	print("[DR SD] 1/4 valid plug given")

	if not (type(drink) == int or type(drink) == str or drink is None):		# break when input type not correct
		return
		
	print("[DR SD] 2/4 correct input type")

	if type(drink) == int:		# get drink name when index given
		drink = drinks[drink]
	
	print("[DR SD] 3/4 got drink name if necessary")
	
	if not (drink in drinks or drink is None):
		return					# break when drink is not available
	
	print("[DR SD] 4/4 drink is available")
	
	plugs[plug] = drink			# set drink on plug


""" MANAGE RECIPES """
def add_drinks(new_drinks):
	""" add new drinks to the drink file
	drinks: a list of the new drinks
	returns True if successfull, False if an error occurred
	"""

	global drinks

	print("[DR AD] adding new drinks")

	file = open(gl.gen_path + "/src/drinks_custom", "a")
	for i in new_drinks:
		file.write(i+"\n")
	file.close()
	drinks.sort()

	print("[DR AD] finished adding new drinks")

	return True


def import_recipe():
	""" opens a file prompt to import a new recipe
	returns True if successfull, False if an error occurred
	"""
	file_path = prompt_file()			# select a file
	print("[DR IR] 1/6 file path:", file_path)

	file = open(file_path, 'r')							# read the file and do a compatability check
	lines = file.readlines()
	file.close()
	for idx, i in enumerate(lines):						# remove trailing newline characters
		if lines[idx].endswith('\n'):
			lines[idx] = lines[idx][:-1]

	print("[DR IR] 2/6 could read file and removed newline characters")

	new_drinks = []
	
	try:											# trying to convert the second param of the instructions to int
		for i in lines[1:]:
			splitted = i.split(',')
			if not splitted[0] in drinks:
				new_drinks.append(splitted[0])
			amount = int(splitted[1])
	except ValueError:
		print("[DR IR] 3/6 ValueError: couldn't convert to int")
		return(False)
	except IndexError:
		print("[DR IR] 3/6 IndexError: couldn't split Commands into drink and amount needed")
		return(False)

	print("[DR IR] 3/6 No faulty units")

	# if necessary, add new drinks to the list
	print("[DR IR] 4/6 These new drinks will be added:", new_drinks)
	success = add_drinks(new_drinks)
	if success:
		print("[DR IR] 4/6 New drinks added successfully")
	else:
		print("[DR IR] 4/6 Error occurred")


	print("[DR IR] 5/6 copy drink to recipe folder")
	try:
		split = file_path.split('/')
		filename = split[-1]
		copyfile(file_path, gl.gen_path + "/src/recipes/" + filename)
	except Exception:
		print("[DR IR] an error occurred while copying the file")
		return False

	# update recipe and drink lists
	update_recipes_and_drinks()
	print("[DR SI] 6/6 update recipes and drinks")

	print("[DR SI] all done")
	return True
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

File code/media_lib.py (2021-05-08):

"""
contains class for graphics, animations and videos
"""

import os
from typing import Sized						# used to scan for files and to execute commands from a commandline
import pygame					# used in Animation-Class for displaying sprites
import pygame.freetype			# used in Button class to show text
import cv2 						# used in Video-Class for displaying videos
import numpy as np 				# used by opencv
import globals as gl			# imports global variables
import tkinter					# used for file prompt to import new recipes
import tkinter.filedialog
from time import time			# used to automatically fade out notifications

class Image:
	""" can be used to easily display single images
	"""

	def __init__(self, path, x, y, width, height, rotation=0, show=True):
		""" create single sprites and easily display them
		- path:	complete path to the image file
		- x:	position on x-axis
		- y:	position on y-axis
		- width:	width of image (doesn't have to be as the original files, image can be stretched)
		- height:	height of image ( -- '' --)
		- rotation=0:	set a certain rotation to the image (optional)
		- show=True:	don't display image directly, when set to False
		"""

		self.file = path
		self.img = pygame.transform.scale(pygame.image.load(path), (width, height))

		# save all parameters
		self.x, self.y = x, y
		if rotation != 0:
			self.img = pygame.transform.rotate(self.img, rotation)
		self.show = show

	def draw(self):
		""" draws the image. no params needed """
		if self.show:
			gl.screen.blit(self.img, (self.x, self.y))


class Button:
	""" class for drawing Buttons with different states """

	def __init__(self, path, img_normal, img_selected, img_disabled, x, y, width, height, direct_load=True, disabled=False, selected=False, rotation=0):
		""" draw single sprites 
		- path: complete path to folder with the files
		- img_normal, img_selected, img_disabled:
			file names for the images
		- x: x-position
		- y: y-position
		- width: width of image
		- height: height of image
		- direct_load=False: set True, when the image should directly be loaded
		- disabled=False: set directly on disabled
		- selected=False: set directly as selected
		"""
		path = path					# save paths
		self.path_normal 	= path + img_normal
		self.path_disabled 	= path + img_disabled
		self.path_selected 	= path + img_selected

		self.x, self.y = x, y						# save x and y coordinates
		self.width, self.height = width, height		# save width and height

		# settings
		self.show = False			# 'turn' image on and off
		self.disabled = disabled	# save if image is disabled (greyed out)
		self.selected = selected	# save if image is selected (somehow marked)
		self.rotation = rotation	# save rotation

		# pygame.Surface objects
		self.img_normal 	= None
		self.img_disabled 	= None
		self.img_selected 	= None

		# text params
		self.show_text = False
		self.text = ""
		self.font = None
		self.font_col = (0, 255, 0)
		self.hor_alignment = 0				# 0 = center, 1 = left, 2 = right
		self.ver_alignment = 0				# 0 = center, 1 = up, 2 = down

		if direct_load == True:
			self.load_image()
	
	def add_text(self, text, font, col, hor_alignment=0, ver_alignment=0):
		""" add text to button
		- text: text to show [String]
		- font: font
		- col: color to use (R, G, B)
		- hor_alignment=0: horizontal alignment (0 = center, 1 = left, 2 = right)
		- ver_alignment=0: vertical alignment (0 = center, 1 = up, 2 = down)
		"""
		self.show_text = True
		self.text = text
		self.font = font
		self.font_col = col
		self.hor_alignment = hor_alignment
		self.ver_alignment = ver_alignment
	
	def load_image(self):
		""" loads image as pygame.Surfaces """
		self.img_normal		= Image(self.path_normal	, self.x, self.y, self.width, self.height, self.rotation)
		self.img_disabled	= Image(self.path_disabled	, self.x, self.y, self.width, self.height, self.rotation)
		self.img_selected	= Image(self.path_selected	, self.x, self.y, self.width, self.height, self.rotation)
		self.show = True

	def set_size(self, *, x=-1, y=-1, w=-1, h=-1):
		""" set new position """
		if x == -1:
			x = self.x
		if y == -1:
			y = self.y
		if w == -1:
			w = self.width
		if h == -1:
			h = self.height

		self.img_normal		= Image(self.path_normal	, x, y, w, h, self.rotation)
		self.img_disabled	= Image(self.path_disabled	, x, y, w, h, self.rotation)
		self.img_selected	= Image(self.path_selected	, x, y, w, h, self.rotation)
	
	def unload_image(self):
		""" deletes pygame.Surface objects """
		self.img_normal 	= None
		self.img_disabled 	= None
		self.img_selected 	= None
		self.show = False
	
	def draw(self):
		"""
		draw the image
		"""

		if self.show:			# draw image based on settings
			if self.disabled:
				self.img_disabled.draw()
			else:
				if self.selected:
					self.img_selected.draw()
				else:
					self.img_normal.draw()
			
			if self.show_text:
				t_x, t_y = self.x, self.y
				textsur, rect = self.font.render(self.text, self.font_col)	# render text
				spacing = 15

				if self.hor_alignment == 0:				# position text based on hor_alignment, ver_alignment, button size and rectangle size of text
					t_x += self.width/2 - rect.width/2
				elif self.hor_alignment == 1:
					t_x += spacing
				elif self.hor_alignment == 2:
					t_x += self.width - rect.width - spacing

				if self.ver_alignment == 0:
					t_y += self.height/2 - rect.height/2
				elif self.ver_alignment == 1:
					t_y += spacing
				elif self.ver_alignment == 2:
					t_y += self.height - rect.height - spacing

				gl.screen.blit(textsur, (t_x, t_y))		# finally blit it
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

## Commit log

2020-12-11 Create Plastic Solenoid Valve.fzpz
2020-12-12 edit Materialliste.md
2020-12-20 removed test frames
2020-12-30 Delete "intro"-files
    Delted all Frames for the intro
2021-01-01 Update medialib.py
    ### [i4] pt.1 rework of frame-by-frame animation
    - redone/updated Animation class (former video class)
    - put image loading in own fucntion / added unload function
    - optimised audio playback
    - optimised playing params
    - optimised play/pause
    - added comments to code
2021-01-03 added video class
    + optimised import
    + made animation fullscreen compatible
    + fixed repeat issue in Ainmation.draw
    + fixed some typos
    [media_lib.py]
2021-01-04 Update media_lib.py
    bug fixes
    [media_lib.py]
2021-01-04 bugfix: animation not playing
    [media_lib.py]
2021-01-04 Update media_lib.py
    whole ton of bug fixes
    [media_lib.py]
2021-01-06 Update media_lib.py
    small bugfix
    [media_lib.py]
2021-01-13 Dokumentation Bestellung der Bauteile hinzugefügt
2021-01-15 Update io_lib.py
    added methods:
    - moved genreal keyboard from main script here
    - read gpio pin
    - write gpio pin
    (including support for win)
2021-01-15 small changes
    - media_lib.py: correction in documentation
    - test.py: small changes
    - vidoe and image files: moved in new directory
    [media_lib.py]
2021-01-20 created prop files
2021-01-20 Update ext_ui_methods_lib.py
    corrected typo in debug info
    [ext_ui_methods_lib.py]
2021-01-21 added and modified prop files
2021-01-21 added Button class
2021-01-25 Update io_lib.py
    added try/except for connecting to serial board
2021-01-26 moved and added prop files
2021-01-26 renamed folder from test-files to props
2021-01-30 Update drinks_lib.py
    fixed newline carrier remove for version < 3.9
    [drinks_lib.py]
2021-02-13 bug fix
    couldn't reset plugs to None (meaning no drink is plugged in)
    [drinks_lib.py]
2021-02-16 Create Raspberry Pi System.md
2021-02-16 Update Raspberry Pi System.md
2021-02-17 Update drinks_lib.py
    - small changes
    - documentation
    - removed some debug prints
2021-02-17 Update arduino_output_test.ino
    documentation
2021-03-17 Update media_lib.py
    small changes; removed some bugs
    [media_lib.py]
2021-03-18 Modification on prop files
    - added triangels
    - got some info about recipes
2021-03-18 Update ext_ui_methods_lib.py
    - worked further on recipe menu
    - small fixes
    [ext_ui_methods_lib.py]
2021-03-18 Update media_lib.py
    added rotation to button class
2021-03-22 Update ext_ui_methods_lib.py
    - documentation for main menu
    - corrected several typos
    - added free lines for formatting
    [ext_ui_methods_lib.py]
2021-03-22 Update paamestia.py
    added shutdown function for raspberry pi (untested)
2021-03-26 Update paamestia.py
    bug fix
    [paamestia.py]
2021-03-26 Update io_lib.py
    enabled keyboard input on raspberry pi
2021-03-26 Update io_lib.py
    bugfixes on keyboard support for raspberry pi
    [io_lib.py]
2021-03-27 changed recipe prop files
2021-03-27 Update ext_ui_methods_lib.py
    reciepes can now be mixed, added recipe output, leaving recipe choose correctly and cleaned up
    [ext_ui_methods_lib.py]
2021-03-27 Update ext_ui_methods_lib.py
    small changes and bug fixes
    [ext_ui_methods_lib.py]
2021-03-27 Update drinks_lib.py
    corrected typos in print statements
    [drinks_lib.py]
2021-03-29 Update media_lib.py
    Deleting VLCVideo-Class, because no longer in use / unnecessary
    [media_lib.py]
2021-03-29 Update media_lib.py
    adapted Button class and Textfield class to new Image class
2021-04-02 Changed number of valves from 7 to 6
2021-04-02 Updated drinks_lib.py and globals.py
    changed the time measuring for mixing and clarified unit for TIME_PER_ML (milliseconds).
    also fixed a bug / mistake in globals.py
    [drinks_lib.py, globals.py]
2021-04-03 added prop files for progress bar
2021-04-04 Update ext_ui_methods_lib.py
    fixed an issue, were the values were given in relative numbers, but absolute numbers are required
    [ext_ui_methods_lib.py]
2021-04-04 deleted the cad file folder from gitignore
    [Mount - Test.stl, Mount.stl, Mount_1 - Test_1.stl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]
2021-04-05 new cad file
    [Mount links 275mm.stl, Mount links 350mm.stl, Mount mitte.stl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]
2021-04-06 small changes / bugfix (forgot trailing newline characters in [UI setup])
    [drinks_lib.py, ext_ui_methods_lib.py]
2021-04-08 scheiß bug beim output
    [io_lib.py]
2021-04-11 scheiß bug beim output und in ui fc bei rezepterstellung gelöst gelöst
    [drinks_lib.py, ext_ui_methods_lib.py, io_lib.py]
2021-04-16 changed credits
    now activated by pressing all buttons or left-shift on keyboard
2021-04-19 reorganized folder structure and added cad-models
    [Brücke (1).stl, Brücke (2).stl, Brücke (3).stl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]
2021-04-19 Update io_lib.py
    removed serial/arduino related stuff
2021-04-21 Update media_lib.py
    added feature to start video on a specific frame
2021-04-21 Update media_lib.py
    fixed bug with maxwidth of textfield
    [media_lib.py]
2021-05-02 documentation / new 3d-model
    [Mount.stl]
2021-05-02 documentation / wiring diagram
    [Schaltplan.fzz]
2021-05-05 Create Mount.stl
    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
    [Mount.stl]
2021-05-06 Update ext_ui_methods_lib.py
    changed background from video to image; bugfixes
    [ext_ui_methods_lib.py]
2021-05-06 Update globals.py
    calibrated
2021-05-06 new prop files
2021-05-07 Create Platzierung Assets.xlsx
    [Platzierung Assets.xlsx]
2021-05-08 Update Platzierung Assets.xlsx
    [Platzierung Assets.xlsx]
2021-05-08 Update media_lib.py
    added set_size function to class Button
2021-05-09 Update io_lib.py
    changed output pins to match with valves left-to-right
2021-05-10 removed prop files
2021-05-11 added cad files
    [Paamestia v142.f3d, Paamestia v142.step]
